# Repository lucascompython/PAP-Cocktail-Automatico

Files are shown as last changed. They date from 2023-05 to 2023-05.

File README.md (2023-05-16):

# PAP-Cocktail-Automático
<div align="center">
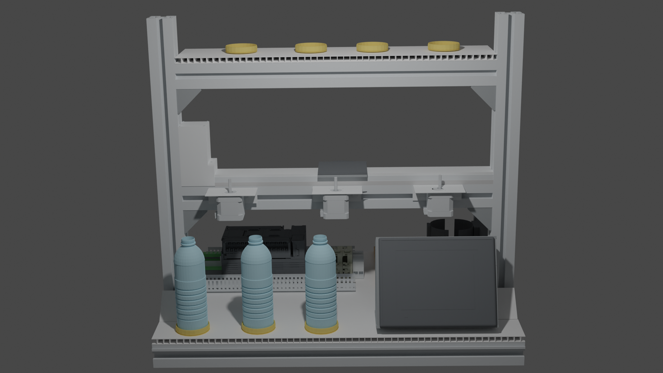
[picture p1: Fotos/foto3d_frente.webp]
    
</div>

## Descrição

Este repositório contém todos os recursos relacionados ao projeto de PAP (Projeto de Aptidão Profissional) de um Cocktail Automático, desenvolvido por: Lucas de Linhares e Roberto Fernandes.  
A PAP é um projeto que desenvolvemos como parte do processo de formação profissional.    Esta inclui vários elementos, como um sistema de mistura de liquidos, um WebSite, bombas peristálticas e mais!

## Instalação de Dependências

```bash
# Clone o repositório
git clone https://github.com/lucascompython/PAP-Cocktail-Automatico

# Entre no diretório do repositório
cd PAP-Cocktail-Automatico/WebSite

# Instale as dependências
pnpm install

# Inicie o servidor de desenvolvimento
pnpm run dev

# Para gerar uma build de produção
pnpm run build

##############

# Instalar as dependências do backend

# Entre no diretório do backend
cd ../Raspberry

# Instale as dependências
pip3 install fastapi uvicorn[standard]

# Iniciar o programa inteiro (incluindo o controle dos motores)
python3 main.py

# Iniciar APENAS o servidor de backend
uvicorn api:app --reload
```

## Licenciamento

Acreditamos no poder do software de código aberto para impulsionar a inovação e tornar o mundo um lugar melhor. Como tal, estamos empenhados em contribuir para a comunidade de código aberto, tornando o nosso trabalho disponível gratuitamente para outros usarem, estudarem e desenvolverem.

O código neste repositório está licenciado sob a GNU General Public License v3.0. Consulte o arquivo `LICENSE` na raiz deste repositório para obter o texto completo da licença.

As fotos, modelos 3D, documentos Word, documentos PowerPoint e PDFs neste repositório estão licenciados sob a Licença Creative Commons Atribuição-CompartilhaIgual 4.0 Internacional. Consulte o arquivo `LICENSE-CC-BY-SA` tambem na raiz deste repositório para obter o texto completo da licença.

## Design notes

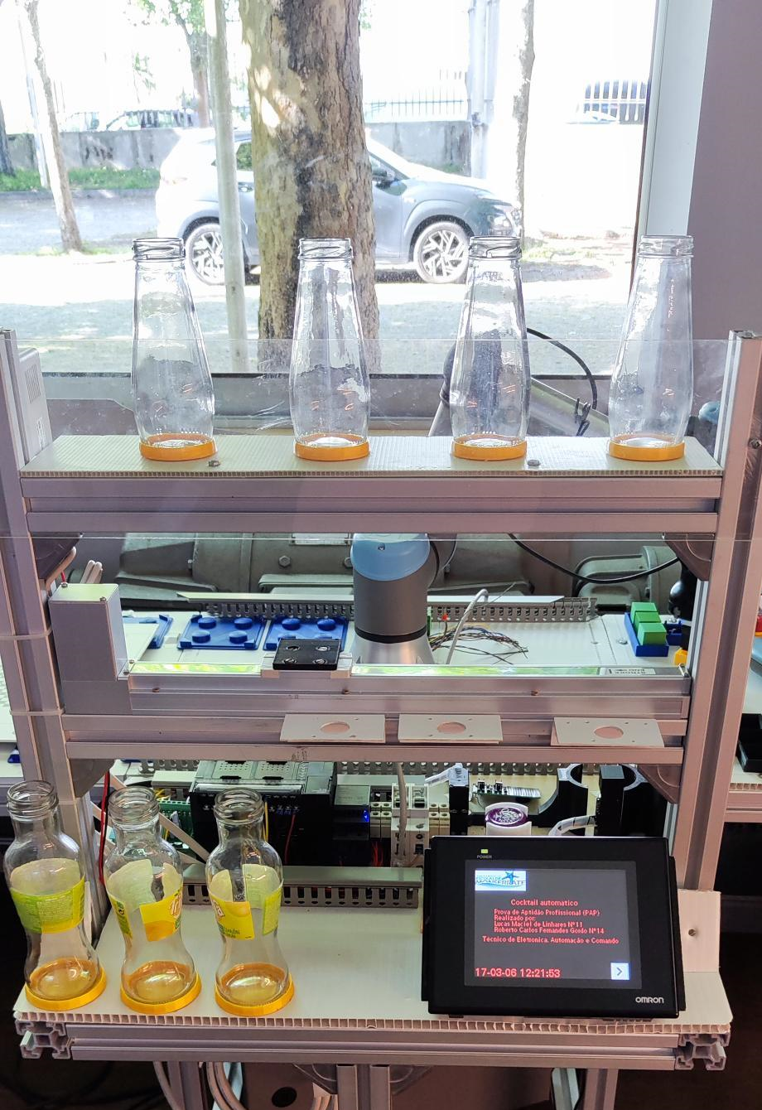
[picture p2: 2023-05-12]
ConsolaPAP/image/foto da pap.bmp

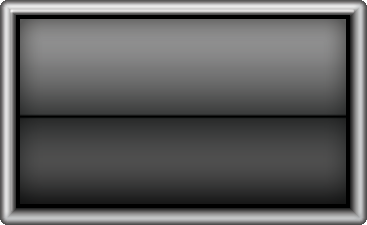
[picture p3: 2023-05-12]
ConsolaPAP/image/button-4-01.bmp

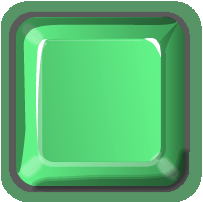
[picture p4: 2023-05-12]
ConsolaPAP/image/button-35-01.bmp

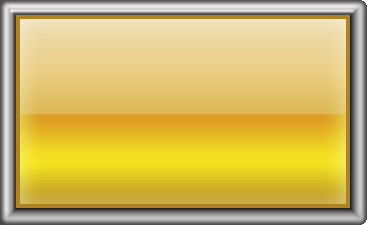
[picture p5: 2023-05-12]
ConsolaPAP/image/button-25-01.bmp

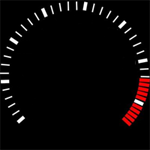
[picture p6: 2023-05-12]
ConsolaPAP/image/METER_1.png

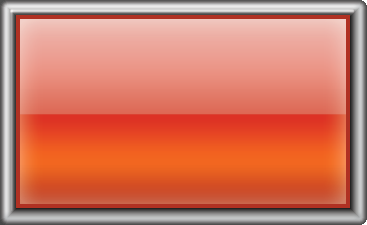
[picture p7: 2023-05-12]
ConsolaPAP/image/button-25-00.bmp

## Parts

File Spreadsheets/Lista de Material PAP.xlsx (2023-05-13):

Material | Quantidade
Autómato OMRON CP1L 30cdr | 1 | un
Consola OMRON NB5Q-TW01B | 1 | un
Disjuntor Unipolar | 2 | un
Fonte de Alimentação 48W 24V 2A | 1 | un
Bornes Siemens | 4 | un
Eixo SMC LEFBT-300-R16P3D / Drive LEFB25T-300 | 1 | un
Fio 0,75mm | 4 | m
Ponteiras Isoladas 0,75mm | 30 | un
Cabo de Rede | 1 | un
Perfil de Aluminio | 4 | m
Tubo de silicode | 3 | m
Acrilico | 0.5 | m^2
Raspberry PI 4 | 1 | un
Fonte de Alimentação Variavel | 1 | un
L298N Motor Driver | 3 | un
Motor Nema 17 | 3 | un
Filamento | 4 | m
Calha | 3 | m
Chapas | 2 | un
Optoacoplador TLP-521 | 4 | un
 |  |  | Material | Quantidade |  | Valor, aquisição (s/IVA) | IVA | Total
 |  |  | Autómato OMRON CP1L 30cdr | 1 | un | 262.96 € | 63.11 € | 326.07 € | 346.00 €
 |  |  | Consola OMRON NB5Q-TW01B | 1 | un | 266.76 € | 64.02 € | 330.78 € | 351.00 €
 |  |  | Disjuntor Unipolar | 2 | un | 4.56 € | 1.09 € | 5.65 € | 6.00 €
 |  |  | Fonte de Alimentação 48W 24V 2A | 1 | un | 14.97 € | 3.59 € | 18.57 € | 19.70 €
 |  |  | Bornes Siemens | 4 | un | 2.89 € | 0.69 € | 3.58 € | 3.80 €
 |  |  | Eixo SMC LEFBT-300-R16P3D / Drive LEFB25T-300 | 1 | un | 801.68 € | 192.40 € | 994.08 € | 1054.84 €
 |  |  | Fio 0,75mm | 4 | m | 0.76 € | 0.18 € | 0.94 € | 1.00 €
 |  |  | Ponteiras Isoladas 0,75mm | 30 | un | 0.46 € | 0.11 € | 0.57 € | 0.60 €
 |  |  | Cabo de Rede | 1 | un | 3.04 € | 0.73 € | 3.77 € | 4.00 €
 |  |  | Perfil de Aluminio | 4 | m | 56.54 € | 13.57 € | 70.11 € | 74.40 €
 |  |  | Tubo de silicode | 3 | m | 12.35 € | 2.96 € | 15.31 € | 16.25 €
 |  |  | Acrilico | 0.5 | m^2 | 2.67 € | 0.64 € | 3.31 € | 3.51 €
 |  |  | Raspberry PI 4 + Cartão SD | 1 | un | 87.01 € | 20.88 € | 107.90 € | 114.49 €
 |  |  | Fonte de Alimentação Variavel | 1 | un | 0.00 € | 0.00 € | 0.00 € | 0.00 €
 |  |  | L298N Motor Driver | 3 | un | 7.30 € | 1.75 € | 9.06 € | 9.61 €
 |  |  | Motor Nema 17 | 3 | un | 15.60 € | 3.74 € | 19.35 € | 20.53 €
 |  |  | Filamento | 4 | m | 5.08 € | 1.22 € | 6.30 € | 6.68 €
 |  |  | Calha | 3 | m | 2.62 € | 0.63 € | 3.25 € | 3.45 €
 |  |  | Chapas | 2 | un | 3.80 € | 0.91 € | 4.71 € | 5.00 €
 |  |  | Optoacoplador | 4 |  | 2.62 € | 0.63 € | 3.25 €
 |  |  | Mão de obra | 160 / 2 | h | * | * | *
 |  |  | Total |  |  | 1551.05 € | 372.25 € | 1923.31 €

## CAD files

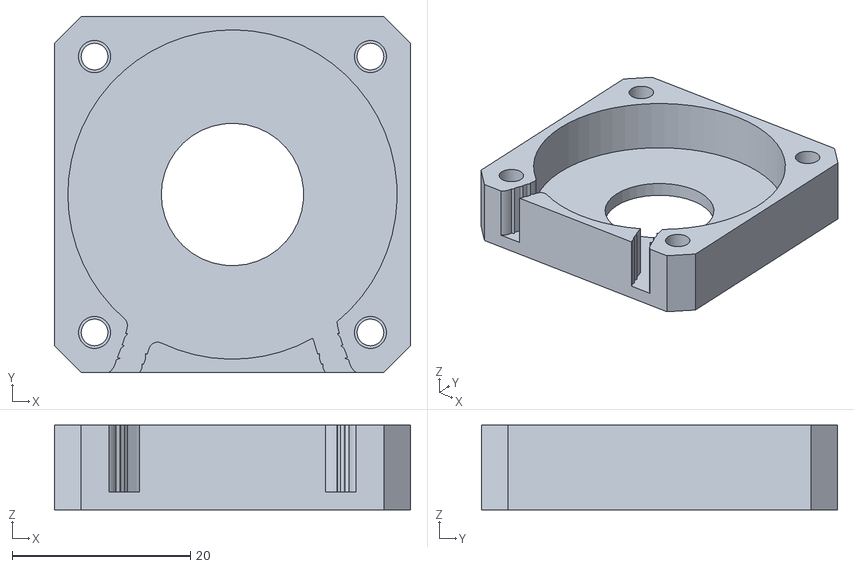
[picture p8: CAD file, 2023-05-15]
Modelos3D/BASE.STL
40.0 x 40.0 x 9.50

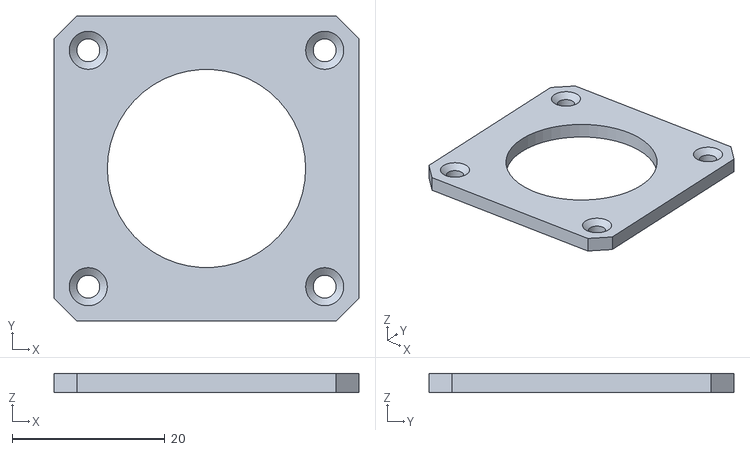
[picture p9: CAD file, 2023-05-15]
Modelos3D/TAMPA.STL
40.0 x 40.0 x 2.50

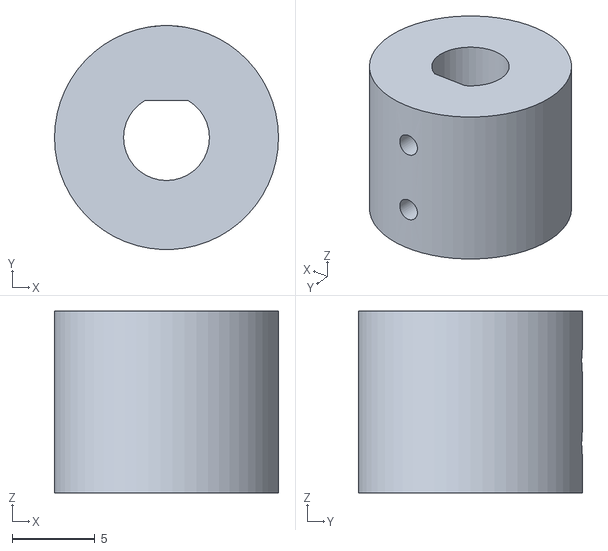
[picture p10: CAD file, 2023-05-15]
Modelos3D/TOPO.STL
13.6 x 13.6 x 11.0

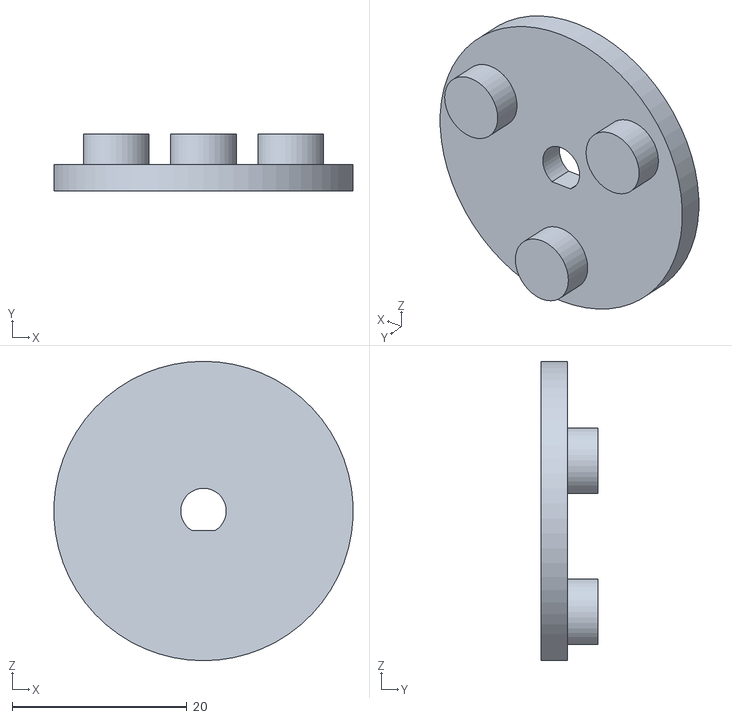
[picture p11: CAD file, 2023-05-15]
Modelos3D/ESTRELA.STL
34.2 x 6.50 x 34.3

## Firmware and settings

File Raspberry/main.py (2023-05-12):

import sys
import threading

import pins
import RPi.GPIO as GPIO
import uvicorn
from api import app

"""
Raspbarry PI PINS

Enviar percentagens para o Autómato:
    8 -> ENTR_1
    10 -> ENTR_2
    12 -> ENTR_3
    16 -> ENTR_4
    18 -> ENTR_5
    22 -> ENTR_6
    24 -> ENTR_7

Receber percentagens do Autómato:
    26 -> 33%
    28 -> 50%
    32 -> 66%
    36 -> 100%
    #38
    40 -> BIT_EXTRA1_OUT no Autómato usado para indicar qual o líquido que está a ser enviado para o Raspberry e quando começar o programa
    7 -> BIT_EXTRA2_OUT no Autómato usado para indicar qual o líquido que está a ser enviado para o Raspberry e quando começar o programa

Para drivers do motor (LN298):
    Motor 1:
        5
        7
        11
        13
    Motor 2:
        15
        19
        21
        23
    Motor 3:
        27
        29
        31
        33

Bits extra:
    35 -> BIT_EXTRA1_IN no Autómato usado para indicar qual o líquido que está a ser enviado para o autómato e quando começar o programa
    37 -> BIT_EXTRA2_IN no Autómato usado para indicar qual o líquido que está a ser enviado para o autómato e quando começar o programa
        
Pos Rasp:
    3 -> "impulso" para fazer o eixo mexer
"""



if __name__ == "__main__":
    try:
        GPIO.setmode(GPIO.BCM)
        # Enviar percentagens para o Autómato
        GPIO.setup(8, GPIO.OUT)
        GPIO.setup(10, GPIO.OUT)
        GPIO.setup(12, GPIO.OUT)
        GPIO.setup(16, GPIO.OUT)
        GPIO.setup(18, GPIO.OUT)
        GPIO.setup(22, GPIO.OUT)
        GPIO.setup(24, GPIO.OUT)

        # Receber percentagens do Autómato
        GPIO.setup(26, GPIO.IN)
        GPIO.setup(28, GPIO.IN)
        GPIO.setup(32, GPIO.IN)
        GPIO.setup(36, GPIO.IN)
        #GPIO.setup(38, GPIO.IN)
        GPIO.setup(40, GPIO.IN)

        # Para drivers do motor (LN298)
        # Motor 1
        GPIO.setup(5, GPIO.OUT)
        GPIO.setup(7, GPIO.OUT)
        GPIO.setup(11, GPIO.OUT)
        GPIO.setup(13, GPIO.OUT)

        # Motor 2
        GPIO.setup(15, GPIO.OUT)
        GPIO.setup(19, GPIO.OUT)
        GPIO.setup(21, GPIO.OUT)
        GPIO.setup(23, GPIO.OUT)

        # Motor 3
        GPIO.setup(27, GPIO.OUT)
        GPIO.setup(29, GPIO.OUT)
        GPIO.setup(31, GPIO.OUT)
        GPIO.setup(33, GPIO.OUT)

        # Bits extra
        GPIO.setup(35, GPIO.IN)
        GPIO.setup(37, GPIO.IN)

        # Posição Raspberry PI (para o eixo)
        GPIO.setup(3, GPIO.OUT)


        server_thread = threading.Thread(target=uvicorn.run, args=(app,), kwargs={"host": "0.0.0.0", "port": 5000}, daemon=True)
        server_thread.start()


        pins.enviar_armazenamento_para_o_automato()

        pins.wait_for_start() 

    except KeyboardInterrupt:
        print("\nInterrunpido pelo utilizador")
        sys.exit(0)
    finally: # garantir que os pinos são libertados
        GPIO.cleanup() 

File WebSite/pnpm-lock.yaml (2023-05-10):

lockfileVersion: '6.0'

dependencies:
  '@emotion/react':
    specifier: ^11.11.0
    version: 11.11.0(@types/react@18.2.6)(react@18.2.0)
  '@emotion/styled':
    specifier: ^11.11.0
    version: 11.11.0(@emotion/react@11.11.0)(@types/react@18.2.6)(react@18.2.0)
  '@mui/material':
    specifier: ^5.12.3
    version: 5.12.3(@emotion/react@11.11.0)(@emotion/styled@11.11.0)(@types/react@18.2.6)(react-dom@18.2.0)(react@18.2.0)
  react:
    specifier: ^18.2.0
    version: 18.2.0
  react-dom:
    specifier: ^18.2.0
    version: 18.2.0(react@18.2.0)

devDependencies:
  '@types/react':
    specifier: ^18.2.6
    version: 18.2.6
  '@types/react-dom':
    specifier: ^18.2.4
    version: 18.2.4
  '@typescript-eslint/eslint-plugin':
    specifier: ^5.59.2
    version: 5.59.2(@typescript-eslint/parser@5.59.2)(eslint@8.40.0)(typescript@5.0.4)
  '@typescript-eslint/parser':
    specifier: ^5.59.2
    version: 5.59.2(eslint@8.40.0)(typescript@5.0.4)
  '@vitejs/plugin-react-swc':
    specifier: ^3.3.0
    version: 3.3.0(vite@4.3.5)
  eslint:
    specifier: ^8.40.0
    version: 8.40.0
  eslint-plugin-react-hooks:
    specifier: ^4.6.0
    version: 4.6.0(eslint@8.40.0)
  eslint-plugin-react-refresh:
    specifier: ^0.4.1
    version: 0.4.1(eslint@8.40.0)
  typescript:
    specifier: ^5.0.4
    version: 5.0.4
  vite:
    specifier: ^4.3.5
    version: 4.3.5

packages:

  /@babel/code-frame@7.21.4:
    resolution: {integrity: sha512-LYvhNKfwWSPpocw8GI7gpK2nq3HSDuEPC/uSYaALSJu9xjsalaaYFOq0Pwt5KmVqwEbZlDu81aLXwBOmD/Fv9g==}
    engines: {node: '>=6.9.0'}
    dependencies:
      '@babel/highlight': 7.18.6
    dev: false

  /@babel/helper-module-imports@7.21.4:
    resolution: {integrity: sha512-orajc5T2PsRYUN3ZryCEFeMDYwyw09c/pZeaQEZPH0MpKzSvn3e0uXsDBu3k03VI+9DBiRo+l22BfKTpKwa/Wg==}
    engines: {node: '>=6.9.0'}
    dependencies:
      '@babel/types': 7.21.5
    dev: false

  /@babel/helper-string-parser@7.21.5:
    resolution: {integrity: sha512-5pTUx3hAJaZIdW99sJ6ZUUgWq/Y+Hja7TowEnLNMm1VivRgZQL3vpBY3qUACVsvw+yQU6+YgfBVmcbLaZtrA1w==}
    engines: {node: '>=6.9.0'}
    dev: false

  /@babel/helper-validator-identifier@7.19.1:
    resolution: {integrity: sha512-awrNfaMtnHUr653GgGEs++LlAvW6w+DcPrOliSMXWCKo597CwL5Acf/wWdNkf/tfEQE3mjkeD1YOVZOUV/od1w==}
    engines: {node: '>=6.9.0'}
    dev: false

  /@babel/highlight@7.18.6:
    resolution: {integrity: sha512-u7stbOuYjaPezCuLj29hNW1v64M2Md2qupEKP1fHc7WdOA3DgLh37suiSrZYY7haUB7iBeQZ9P1uiRF359do3g==}
    engines: {node: '>=6.9.0'}
    dependencies:
      '@babel/helper-validator-identifier': 7.19.1
      chalk: 2.4.2
      js-tokens: 4.0.0
    dev: false

  /@babel/runtime@7.21.5:
    resolution: {integrity: sha512-8jI69toZqqcsnqGGqwGS4Qb1VwLOEp4hz+CXPywcvjs60u3B4Pom/U/7rm4W8tMOYEB+E9wgD0mW1l3r8qlI9Q==}
    engines: {node: '>=6.9.0'}
    dependencies:
      regenerator-runtime: 0.13.11
    dev: false

  /@babel/types@7.21.5:
    resolution: {integrity: sha512-m4AfNvVF2mVC/F7fDEdH2El3HzUg9It/XsCxZiOTTA3m3qYfcSVSbTfM6Q9xG+hYDniZssYhlXKKUMD5m8tF4Q==}
    engines: {node: '>=6.9.0'}
    dependencies:
      '@babel/helper-string-parser': 7.21.5
      '@babel/helper-validator-identifier': 7.19.1
      to-fast-properties: 2.0.0
    dev: false

  /@emotion/babel-plugin@11.11.0:
    resolution: {integrity: sha512-m4HEDZleaaCH+XgDDsPF15Ht6wTLsgDTeR3WYj9Q/k76JtWhrJjcP4+/XlG8LGT/Rol9qUfOIztXeA84ATpqPQ==}
    dependencies:
      '@babel/helper-module-imports': 7.21.4
      '@babel/runtime': 7.21.5
      '@emotion/hash': 0.9.1
      '@emotion/memoize': 0.8.1
      '@emotion/serialize': 1.1.2
      babel-plugin-macros: 3.1.0
      convert-source-map: 1.9.0
      escape-string-regexp: 4.0.0
      find-root: 1.1.0
      source-map: 0.5.7
      stylis: 4.2.0
    dev: false

  /@emotion/cache@11.11.0:
    resolution: {integrity: sha512-P34z9ssTCBi3e9EI1ZsWpNHcfY1r09ZO0rZbRO2ob3ZQMnFI35jB536qoXbkdesr5EUhYi22anuEJuyxifaqAQ==}
    dependencies:
      '@emotion/memoize': 0.8.1
      '@emotion/sheet': 1.2.2
      '@emotion/utils': 1.2.1
      '@emotion/weak-memoize': 0.3.1
      stylis: 4.2.0
    dev: false

  /@emotion/hash@0.9.1:
    resolution: {integrity: sha512-gJB6HLm5rYwSLI6PQa+X1t5CFGrv1J1TWG+sOyMCeKz2ojaj6Fnl/rZEspogG+cvqbt4AE/2eIyD2QfLKTBNlQ==}
    dev: false

  /@emotion/is-prop-valid@1.2.1:
    resolution: {integrity: sha512-61Mf7Ufx4aDxx1xlDeOm8aFFigGHE4z+0sKCa+IHCeZKiyP9RLD0Mmx7m8b9/Cf37f7NAvQOOJAbQQGVr5uERw==}
    dependencies:
      '@emotion/memoize': 0.8.1
    dev: false

  /@emotion/memoize@0.8.1:
    resolution: {integrity: sha512-W2P2c/VRW1/1tLox0mVUalvnWXxavmv/Oum2aPsRcoDJuob75FC3Y8FbpfLwUegRcxINtGUMPq0tFCvYNTBXNA==}
    dev: false
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

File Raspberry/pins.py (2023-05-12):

from time import sleep
from typing import Optional

import orjson
import RPi.GPIO as GPIO

informacao_enviada = False
VEL = 0.0005 # quanto menor, mais rápido

def obter_percentagem_do_autómato() -> int:
    if GPIO.input(26):
        return 33
    elif GPIO.input(28):
        return 50
    elif GPIO.input(32):
        return 66
    elif GPIO.input(36):
        return 100
    elif GPIO.input(32) and GPIO.input(36):
        return 0



def mover_eixo(pos: int):
    GPIO.output(3, GPIO.HIGH)

    if pos == 1:
        GPIO.output(22, GPIO.HIGH)
        GPIO.output(24, GPIO.HIGH)
    
    elif pos == 2:
        GPIO.output(22, GPIO.HIGH)
        GPIO.output(24, GPIO.LOW)
    
    elif pos == 3:
        GPIO.output(22, GPIO.LOW)
        GPIO.output(24, GPIO.HIGH)
    
    elif pos == 4:
        GPIO.output(22, GPIO.LOW)
        GPIO.output(24, GPIO.LOW)
    





def run_motores(voltas: int, motor: int):

    pin1 = 0
    pin2 = 0
    pin3 = 0
    pin4 = 0

    if motor == 1:
        pin1 = 5
        pin2 = 7
        pin3 = 11
        pin4 = 13
    elif motor == 2:
        pin1 = 15
        pin2 = 19
        pin3 = 21
        pin4 = 23
    elif motor == 3:
        pin1 = 27
        pin2 = 29
        pin3 = 31
        pin4 = 33


    for _ in range(round((voltas * 200) / 4)):
        GPIO.output(pin1,GPIO.HIGH)
        GPIO.output(pin2,GPIO.HIGH)
        GPIO.output(pin3,GPIO.LOW)
        GPIO.output(pin4,GPIO.LOW)
        sleep(VEL)

        GPIO.output(pin1,GPIO.LOW)
        GPIO.output(pin2,GPIO.HIGH)
        GPIO.output(pin3,GPIO.HIGH)
        GPIO.output(pin4,GPIO.LOW)
        sleep(VEL)

        GPIO.output(pin1,GPIO.LOW)
        GPIO.output(pin2,GPIO.LOW)
        GPIO.output(pin3,GPIO.HIGH)
        GPIO.output(pin4,GPIO.HIGH)
        sleep(VEL)

        GPIO.output(pin1,GPIO.HIGH)
        GPIO.output(pin2,GPIO.LOW)
        GPIO.output(pin3,GPIO.LOW)
        GPIO.output(pin4,GPIO.HIGH)
        sleep(VEL)


    


def check_bits_e_enviar_liquido(liquido: int):
    if GPIO.input(26): #33%
        voltas = 20 
        run_motores(voltas, liquido)

    elif GPIO.input(28): #50%
        voltas = 30
        run_motores(voltas, liquido)

    elif GPIO.input(32): #66%
        voltas = 40
        run_motores(voltas, liquido)

    elif GPIO.input(36): #100%
        voltas = 60
        run_motores(voltas, liquido)


    elif GPIO.input(32) and GPIO.input(36): #0%
        pass


def enviar_armazenamento_para_o_automato(just_percentages: bool = False) -> Optional[dict[str]: list[int]]:

    try:
        with open("armazenamento.json", "rb") as f:
            armazenamento = orjson.loads(f.read())

    except FileNotFoundError:
        print("Dados do armazenamento não encontrados\nCriando dados do armazenamento e assumindo que o armazenamento está cheio...")
        armazenamento = {
            "percentagens": [100, 100, 100]
        }

    if just_percentages: return armazenamento

    bin_liquido1 = bin(armazenamento["percentagens"][0])[2:]
    bin_liquido2 = bin(armazenamento["percentagens"][1])[2:]
    bin_liquido3 = bin(armazenamento["percentagens"][2])[2:]

    # adicionar zeros à esquerda para ficar com 7 bits
    bin_liquido1 = "0" * (7 - len(bin_liquido1)) + bin_liquido1
    bin_liquido2 = "0" * (7 - len(bin_liquido2)) + bin_liquido2
    bin_liquido3 = "0" * (7 - len(bin_liquido3)) + bin_liquido3

    # enviar bits para o autómato

    #liquido1
    GPIO.output(35, GPIO.LOW)
    GPIO.output(37, GPIO.LOW)

    GPIO.output(8, int(bin_liquido1[0]))
    GPIO.output(10, int(bin_liquido1[1]))
    GPIO.output(12, int(bin_liquido1[2]))
    GPIO.output(16, int(bin_liquido1[3]))
    GPIO.output(18, int(bin_liquido1[4]))
    GPIO.output(22, int(bin_liquido1[5]))
    GPIO.output(24, int(bin_liquido1[6]))

    sleep(0.07)
    #liquido2
    GPIO.output(35, GPIO.LOW) # para indicar que o liquido2 está a ser enviado
    GPIO.output(37, GPIO.HIGH)

    GPIO.output(8, int(bin_liquido2[0]))
    GPIO.output(10, int(bin_liquido2[1]))
    GPIO.output(12, int(bin_liquido2[2]))
    GPIO.output(16, int(bin_liquido2[3]))
    GPIO.output(18, int(bin_liquido2[4]))
    GPIO.output(22, int(bin_liquido2[5]))
    GPIO.output(24, int(bin_liquido2[6]))

    sleep(0.07)

    #liquido3
    GPIO.output(35, GPIO.HIGH) # para indicar que o liquido2 não está a ser enviado
    GPIO.output(37, GPIO.LOW) # para indicar que o liquido3 está a ser enviado

    GPIO.output(8, int(bin_liquido3[0]))
    GPIO.output(10, int(bin_liquido3[1]))
    GPIO.output(12, int(bin_liquido3[2]))
    GPIO.output(16, int(bin_liquido3[3]))
    GPIO.output(18, int(bin_liquido3[4]))
    GPIO.output(22, int(bin_liquido3[5]))
    GPIO.output(24, int(bin_liquido3[6]))

    sleep(0.07)

    # desligar tudo
    GPIO.output(35, GPIO.LOW) 

    GPIO.output(8, GPIO.LOW)
    GPIO.output(10, GPIO.LOW)
    GPIO.output(12, GPIO.LOW)
    GPIO.output(16, GPIO.LOW)
    GPIO.output(18, GPIO.LOW)
    GPIO.output(22, GPIO.LOW)
    GPIO.output(24, GPIO.LOW)


    #GPIO.output(40, GPIO.LOW) # para indicar que o liquido3 não está a ser enviado

    if not informacao_enviada:
        informacao_enviada = True
    
    else:
        # atualizar armazenamento
        armazenamento["percentagens"][0] -= obter_percentagem_do_autómato()
        armazenamento["percentagens"][1] -= obter_percentagem_do_autómato()
        armazenamento["percentagens"][2] -= obter_percentagem_do_autómato()

        with open("armazenamento.json", "wb") as f:
            f.write(orjson.dumps(armazenamento))







def wait_for_start():
    while True:

        if GPIO.input(40) and GPIO.input(7):
            enviar_armazenamento_para_o_automato()
            sleep(21) # tempo que o robo demora a colocar a garrafa no eixo

            #liquido1
            if not GPIO.input(40) and not GPIO.input(7):
                check_bits_e_enviar_liquido(1)

            #liquido2
            if GPIO.input(40) and not GPIO.input(7):
                check_bits_e_enviar_liquido(2)

            #liquido3
            if not GPIO.input(40) and GPIO.input(7):
                check_bits_e_enviar_liquido(3)

        sleep(0.001)

if __name__ == "__main__":
    import sys
    sys.stderr.write("Este programa não deve ser executado diretamente\nUtilize o programa 'main.py'")
    exit(1)

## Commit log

2023-05-11 Adicionar butão start, foto modelo 3d e mudar prop
2023-05-12 Adicionar raspberry pi, eixo origem
2023-05-13 Upload relatório e spreadsheets
    [Lista de Material PAP.xlsx, cronograma.xlsx]
2023-05-15 Corrigir circuito do raspberry pi
    [BASE.STL, ESTRELA.STL, TAMPA.STL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]
2023-05-16 Substituir "mao de obra" para "horas homem"
